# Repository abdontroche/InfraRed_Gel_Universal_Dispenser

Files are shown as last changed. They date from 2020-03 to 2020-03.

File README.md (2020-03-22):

=================================
This project pretends to be a open source device that could help people fighting against the COVID-19.
# Who are we?
*Estimados Miembros: Este grupo está conformado por alumnos, profesores y egresados de la FP-UNA y tiene por objetivo pensar, formular y realizar acciones concretas ante esta situación adversa que vivimos en el país con respecto al coronavirus COVID-19. Iniciamos con gente del área de electrónica e informática pero no estamos cerrados de ninguna manera. El trabajo es voluntario y sin fines de lucro. A hombros de gigantes enfrentaremos mejor las adversidades.*

Dear Members: This group is made up of students, professors and graduates of the FP-UNA and its objective is to think, formulate and carry out concrete actions in the face of this adverse situation that we are experiencing in the country with respect to the COVID-19 coronavirus. We started with people from the electronics and computing area but we are not closed in any way. The work is voluntary and non-profit. On the shoulders of giants we will better face adversities.

Team FP-UNA/COVID

# What we want to achieve?
The board is based on the website called [www.electroschematics.com](www.electroschematics.com) and the project is called [Automatic soap dispenser IR proximity sensor](https://www.electroschematics.com/automatic-soap-dispenser-ir-proximity-sensor/).

We want to use this board and use to dispense gel alcohol adapting it on differents bottles. 

# What we will find inside this repository?

Fist to all we will find the board.

The Board was designed using the software [KiCad 5.1.2](https://www.kicad-pcb.org)

The components are chosen by the existence on the Paraguay electronics componentes market.

## The schmematic

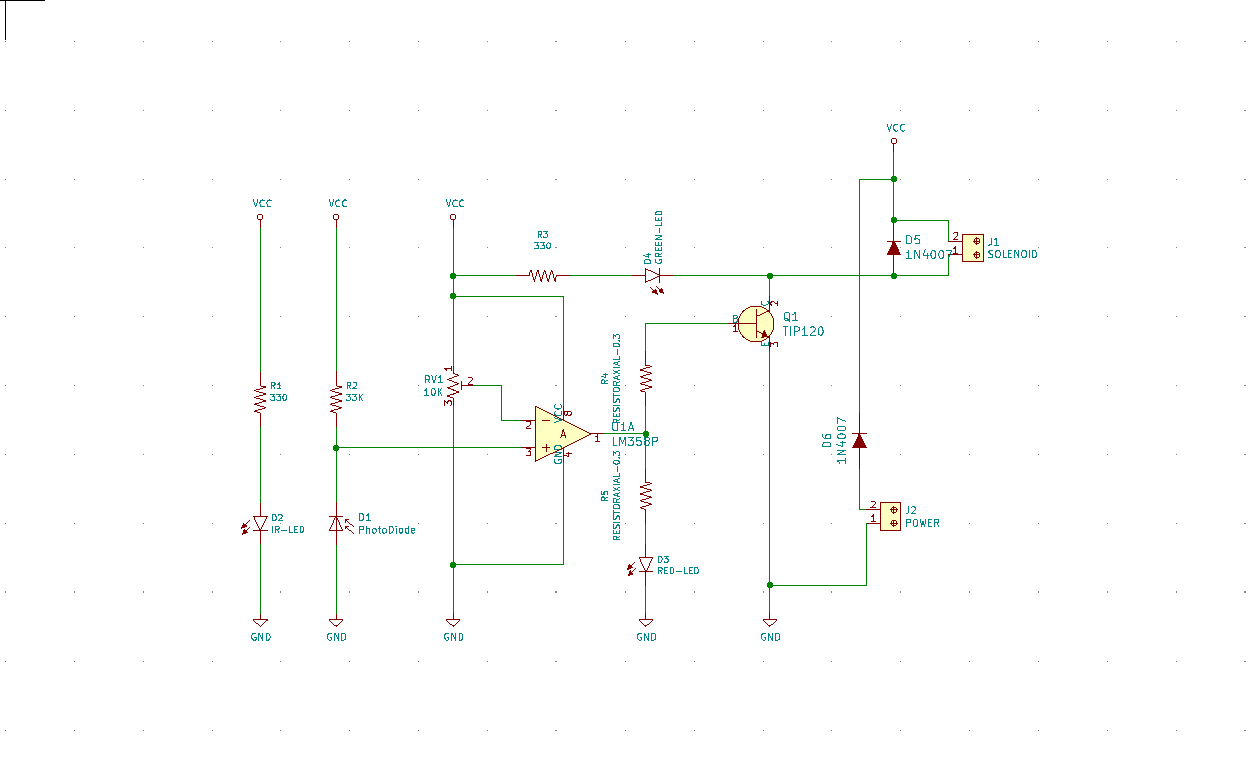
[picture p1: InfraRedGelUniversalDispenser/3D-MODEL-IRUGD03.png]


## The board

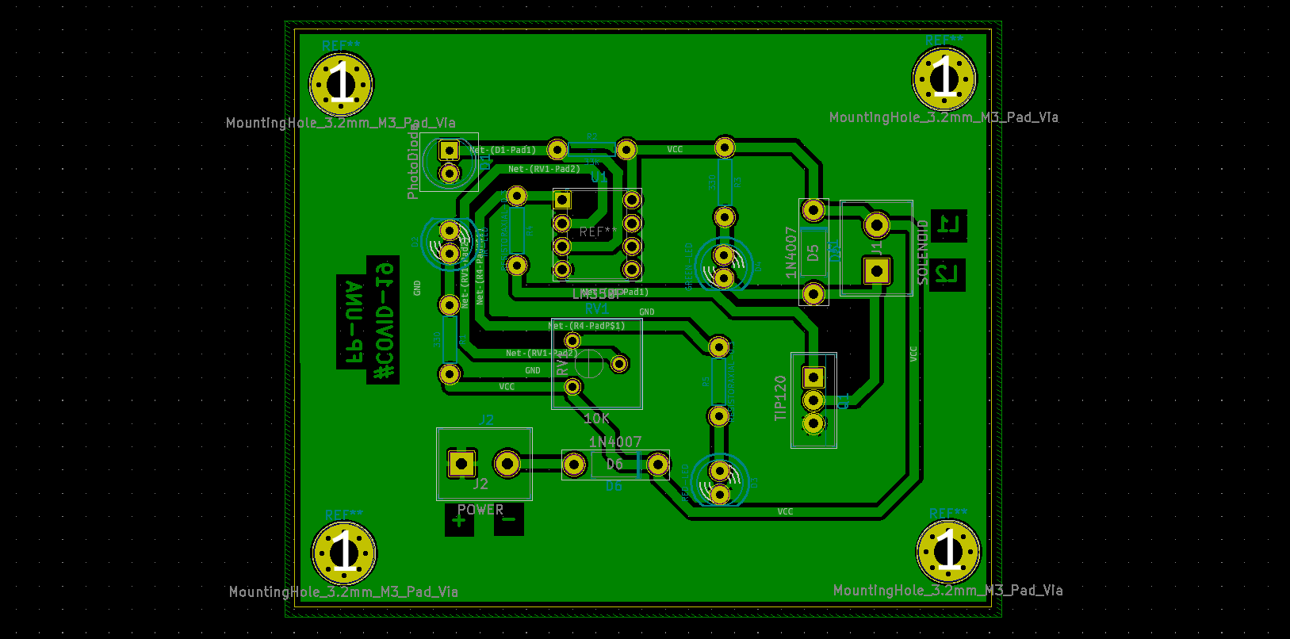
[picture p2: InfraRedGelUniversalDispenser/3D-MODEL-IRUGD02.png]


## Bill Of Materials
This is the file of the [BOM](InfraRedGelUniversalDispenser/bom/ibom.html)
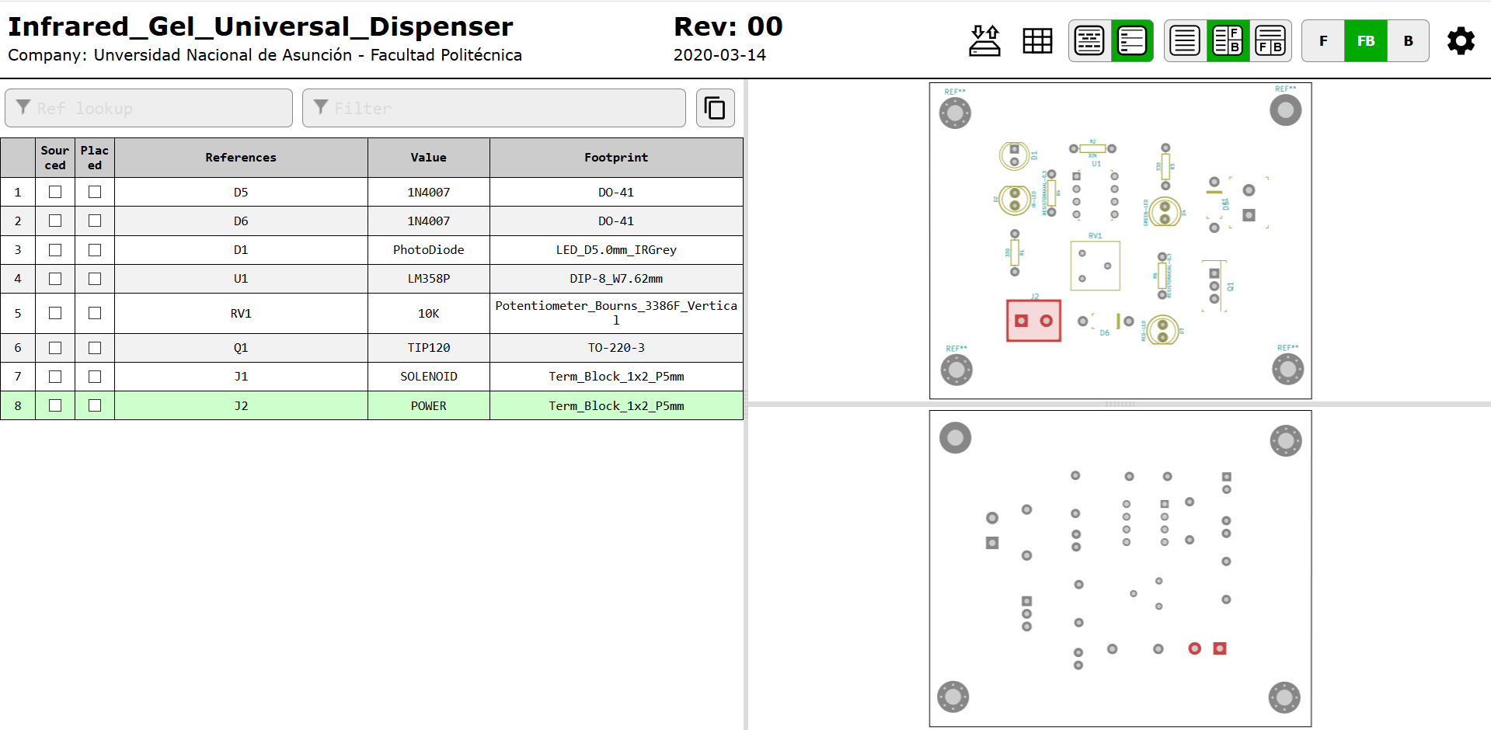
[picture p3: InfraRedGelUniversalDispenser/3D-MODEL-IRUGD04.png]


## The 3D models

You will find the board 3D model in the STP format in order you can choose the software you want to develope the mechanism with.

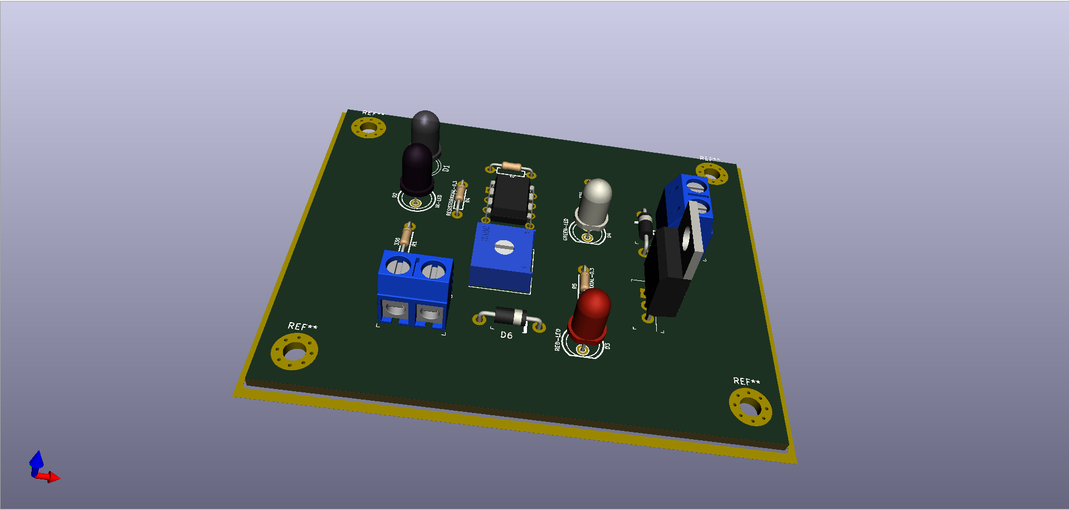
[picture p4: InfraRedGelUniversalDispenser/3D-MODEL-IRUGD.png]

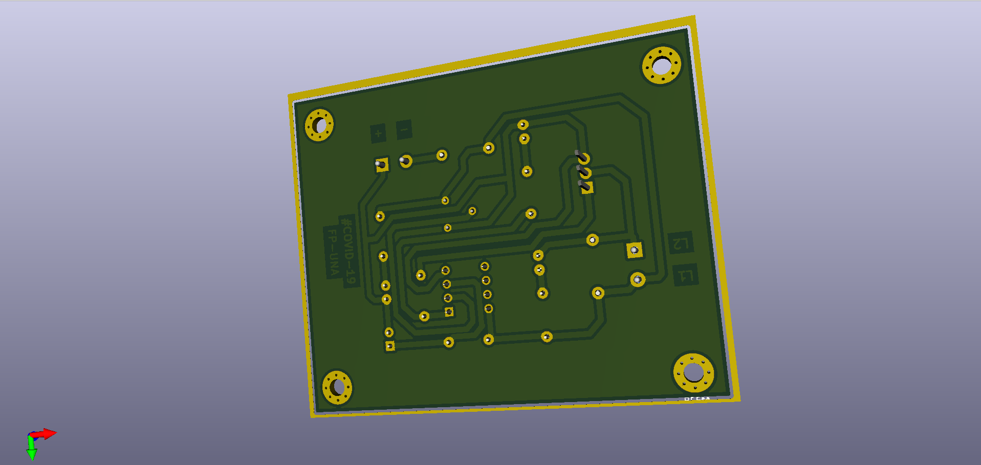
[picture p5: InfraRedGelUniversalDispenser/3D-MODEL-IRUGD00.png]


### Desing the mechanism using [Fusion 360](https://www.autodesk.com/products/fusion-360/students-teachers-educators)

#### Electronic board

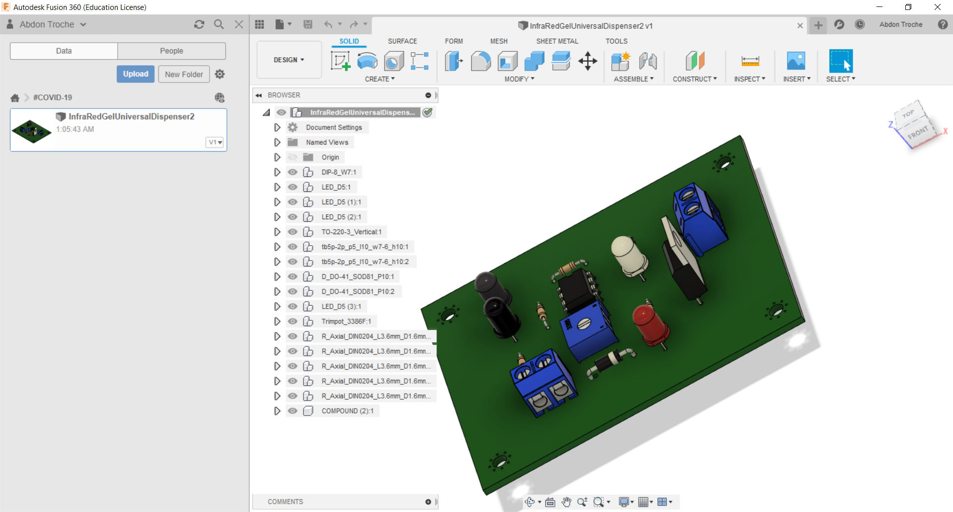
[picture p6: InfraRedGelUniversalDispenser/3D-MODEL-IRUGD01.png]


#### [Dispenser mecanism](InfraRedGelUniversalDispenser/CustomizedSolenoid v5.step)

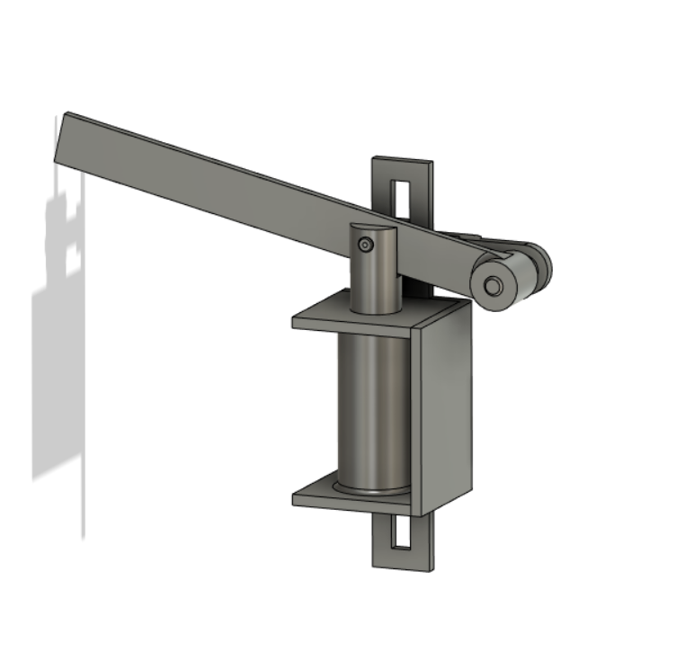
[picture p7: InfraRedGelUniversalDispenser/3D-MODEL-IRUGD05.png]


#### [Gel alcohol bottle or soap bottle dispenser](https://grabcad.com/library/soap-dispenser-5)

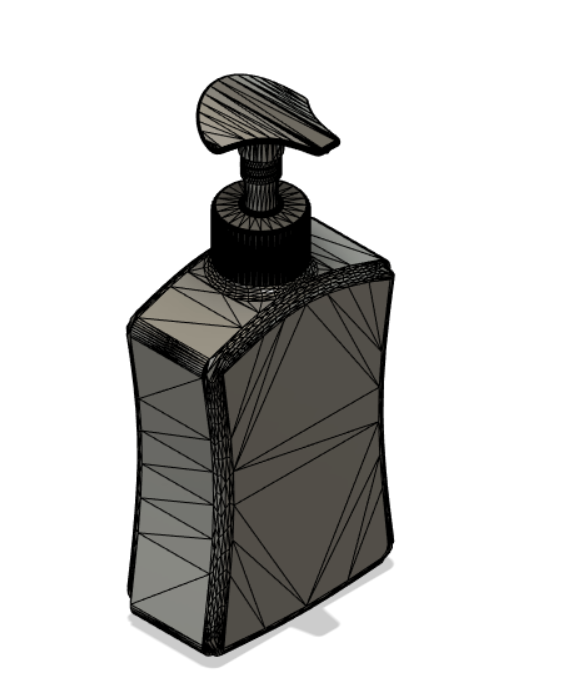
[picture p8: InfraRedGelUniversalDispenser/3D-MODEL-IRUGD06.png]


#### Fisrt assembly

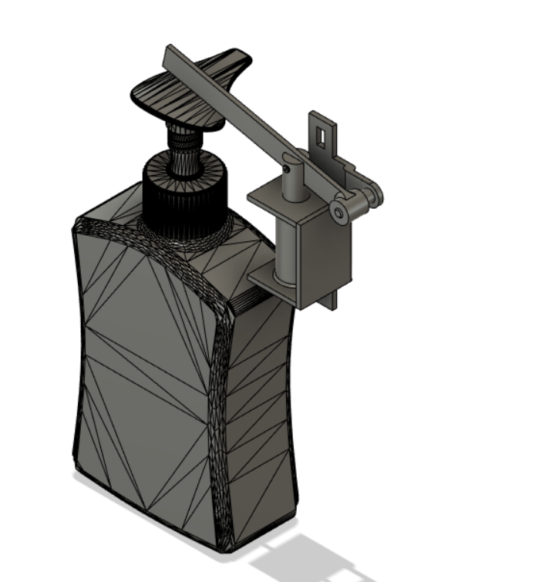
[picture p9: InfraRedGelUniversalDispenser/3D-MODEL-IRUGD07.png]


#### Second assembly

File of the prototipe "InfraRedGelUniversalDispenserDevice v17.step"

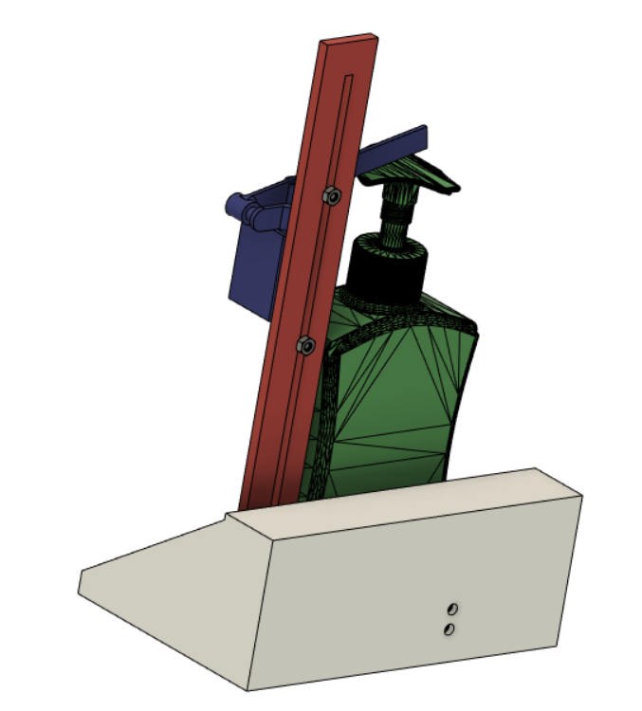
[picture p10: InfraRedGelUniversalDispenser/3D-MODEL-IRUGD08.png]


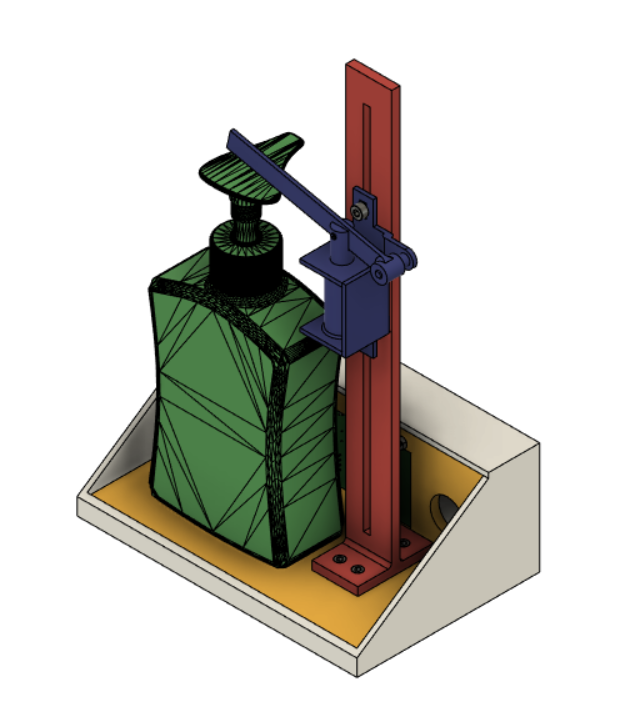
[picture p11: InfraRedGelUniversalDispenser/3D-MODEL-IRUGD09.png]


# This is another version of the board
## The schmematic

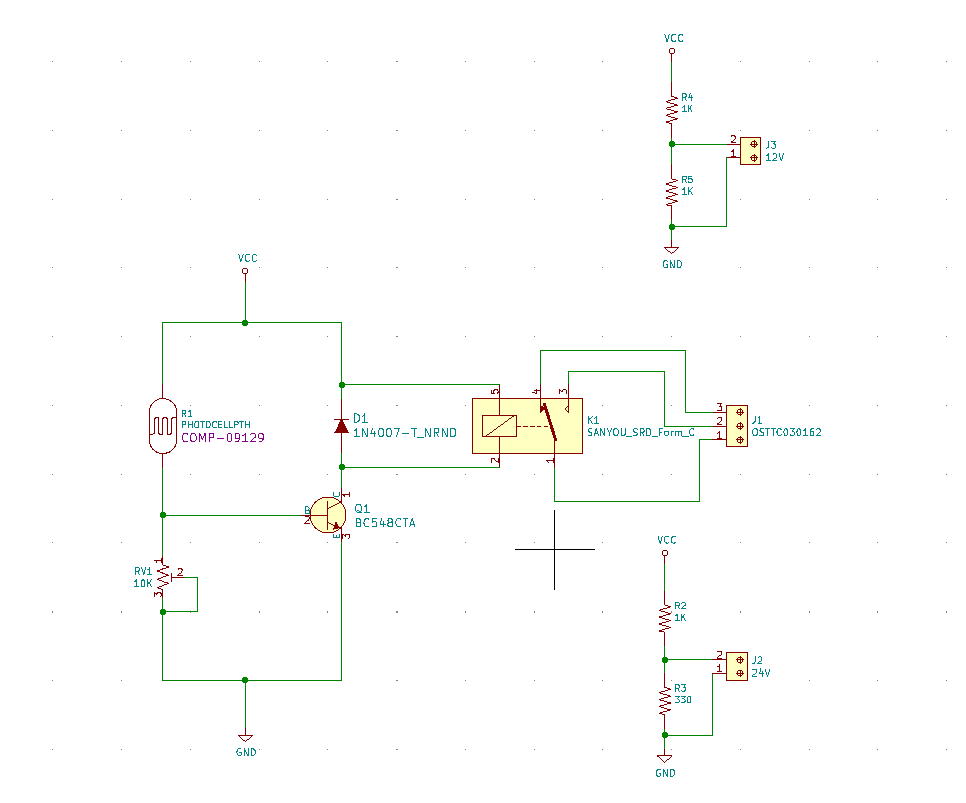
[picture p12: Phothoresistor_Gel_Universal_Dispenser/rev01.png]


## The board

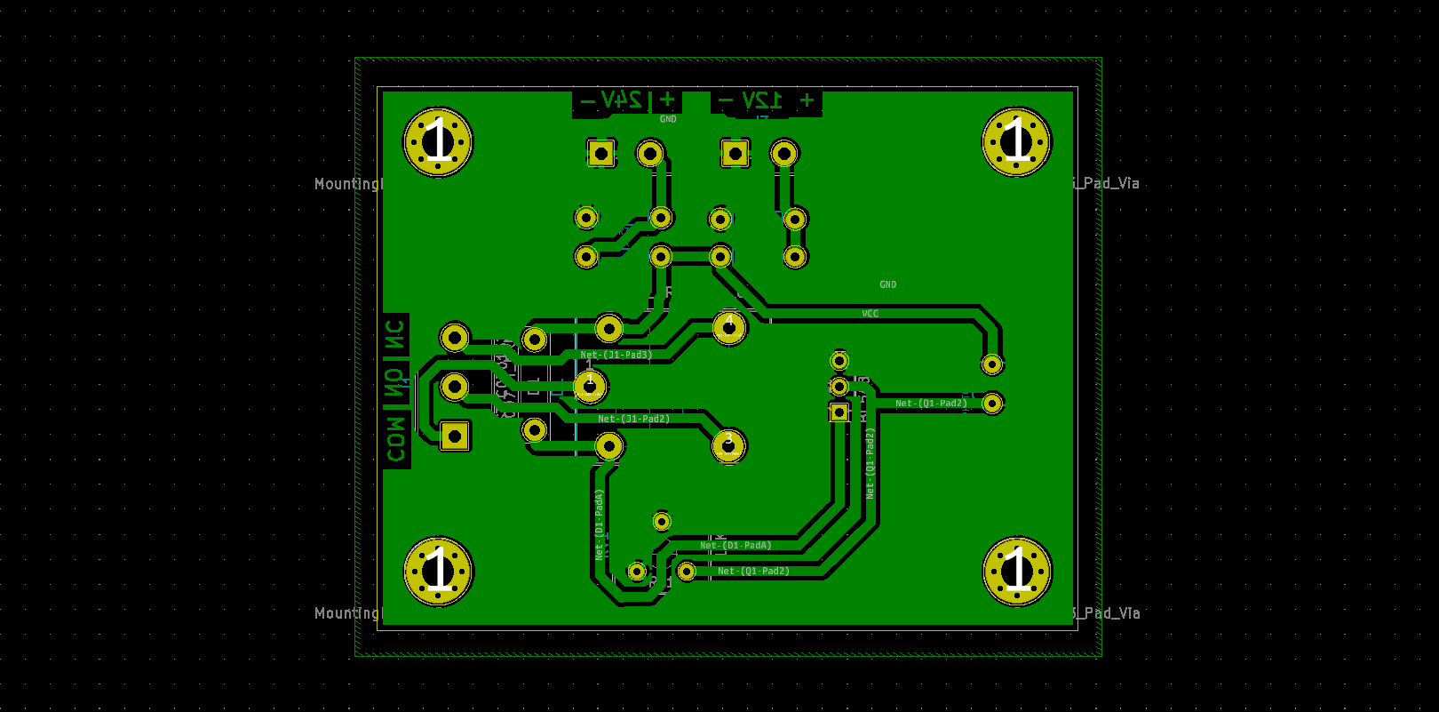
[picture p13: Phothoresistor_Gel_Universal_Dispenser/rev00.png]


## Bill Of Materials

## The 3D models

You will find the board 3D model in the STP format in order you can choose the software you want to develope the mechanism with.

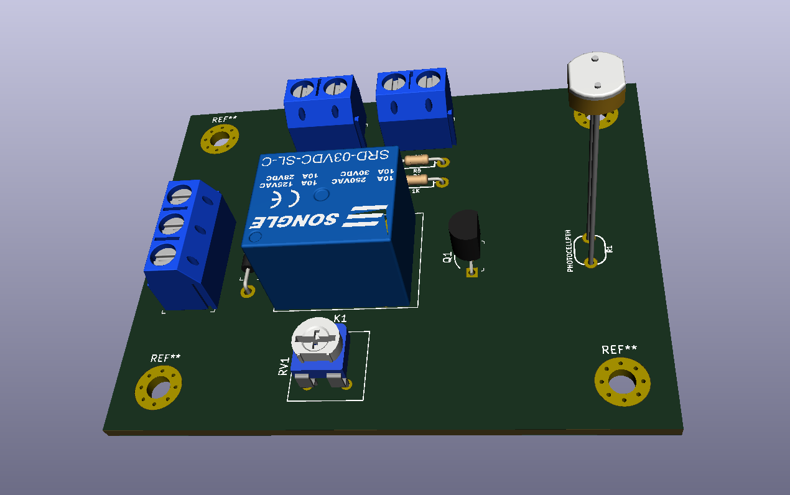
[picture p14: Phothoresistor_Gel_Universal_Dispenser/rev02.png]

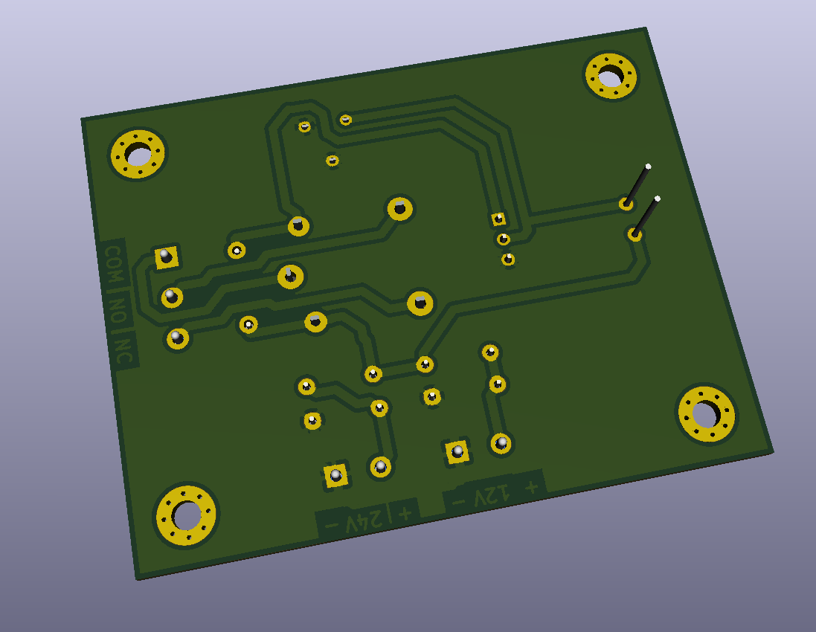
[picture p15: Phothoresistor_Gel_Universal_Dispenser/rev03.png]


### Desing the mechanism using [Fusion 360](https://www.autodesk.com/products/fusion-360/students-teachers-educators)

#### Electronic board

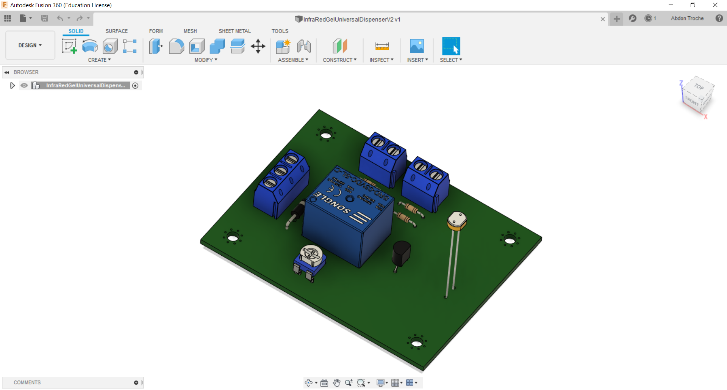
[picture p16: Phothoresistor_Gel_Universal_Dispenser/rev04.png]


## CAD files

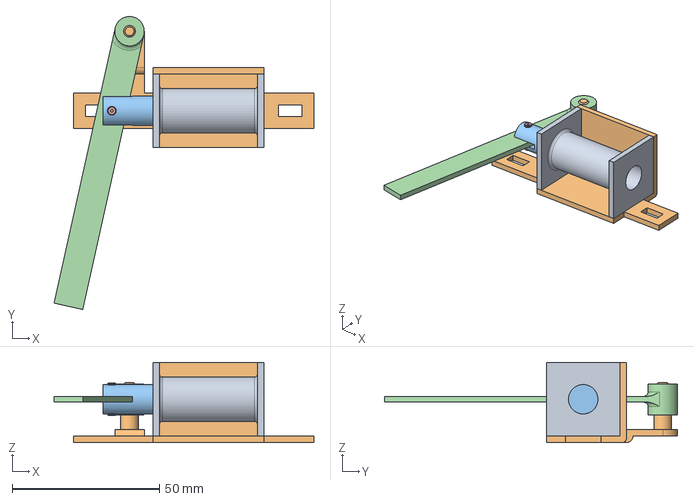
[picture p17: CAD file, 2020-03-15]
InfraRedGelUniversalDispenser/CustomizedSolenoid v5.step
88.2 x 99.4 x 27.2 mm

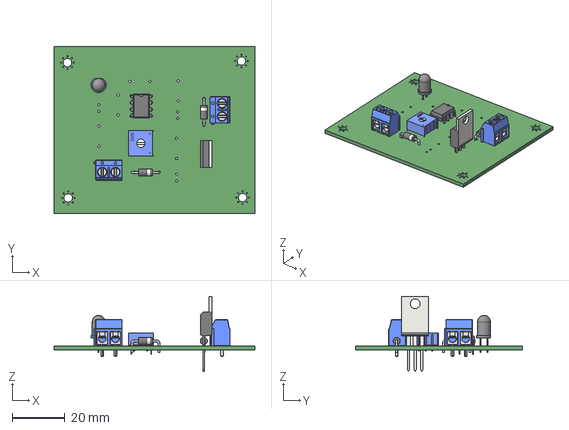
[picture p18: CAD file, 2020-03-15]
InfraRedGelUniversalDispenser/InfraRedGelUniversalDispenser.step
76.4 x 63.3 x 28.5 mm

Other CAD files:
InfraRedGelUniversalDispenser/InfraRedGelUniversalDispenser2 v1.f3d
Phothoresistor_Gel_Universal_Dispenser/Phothoresistor_Gel_Universal_Dispenser.f3d

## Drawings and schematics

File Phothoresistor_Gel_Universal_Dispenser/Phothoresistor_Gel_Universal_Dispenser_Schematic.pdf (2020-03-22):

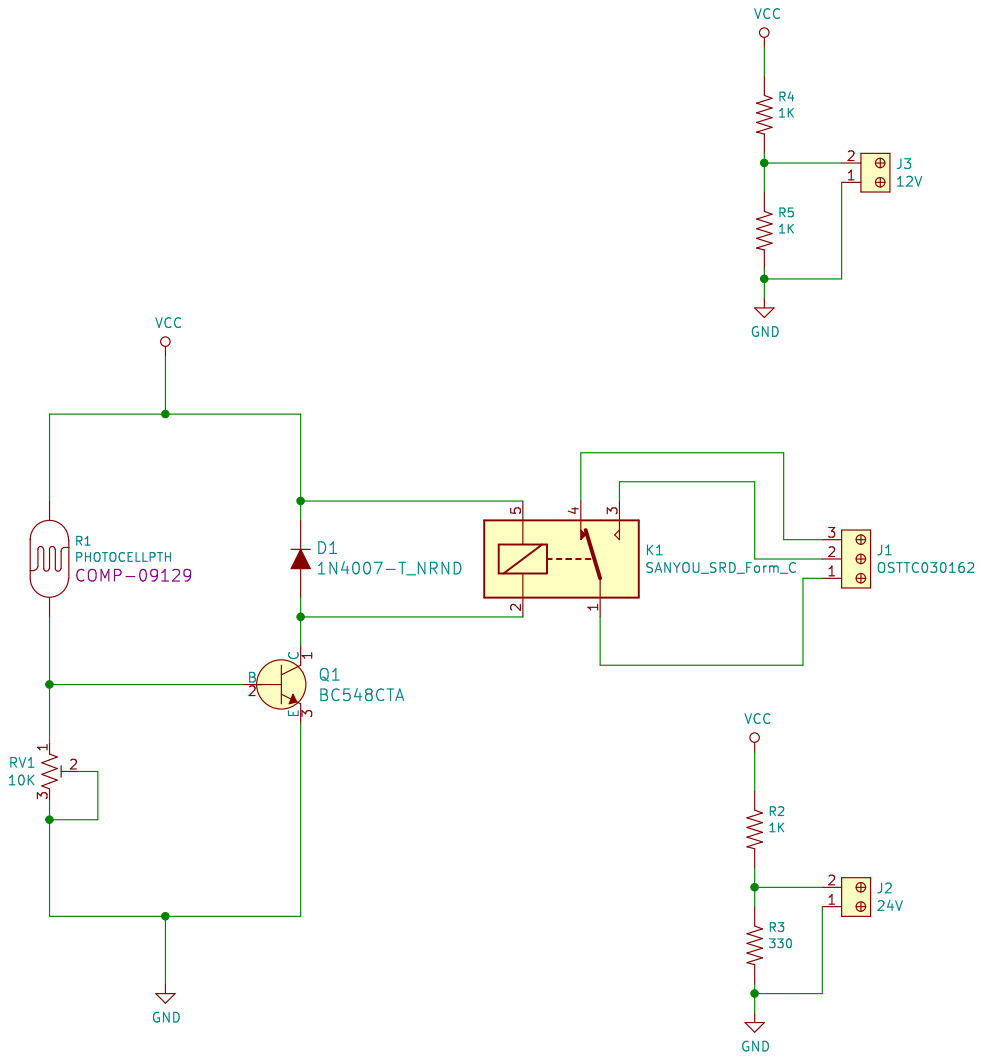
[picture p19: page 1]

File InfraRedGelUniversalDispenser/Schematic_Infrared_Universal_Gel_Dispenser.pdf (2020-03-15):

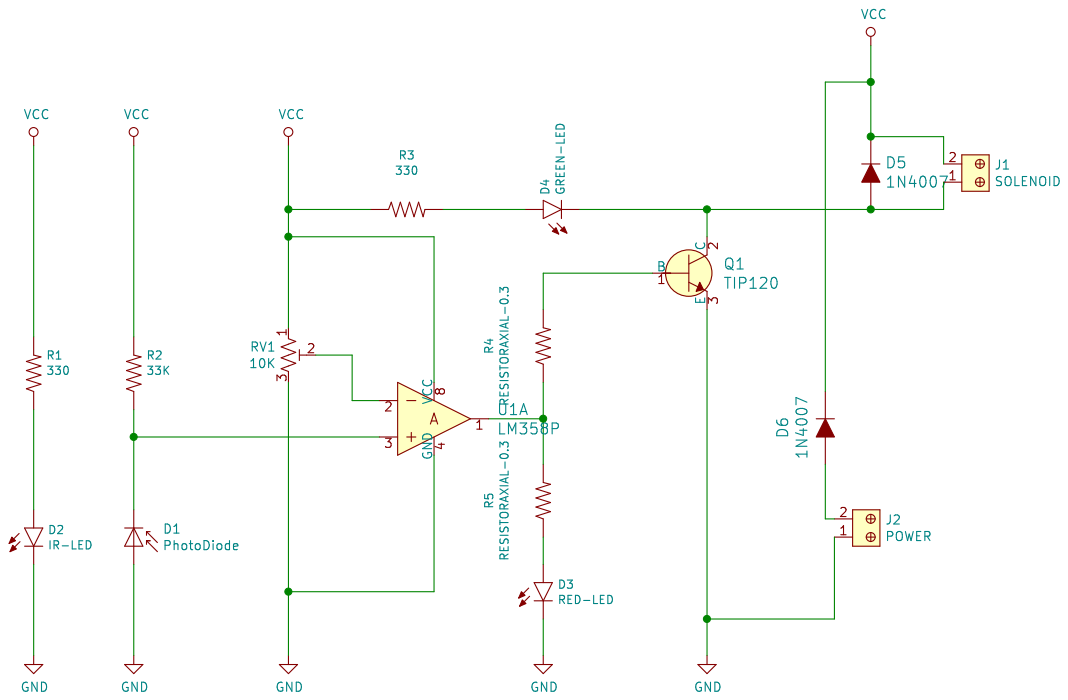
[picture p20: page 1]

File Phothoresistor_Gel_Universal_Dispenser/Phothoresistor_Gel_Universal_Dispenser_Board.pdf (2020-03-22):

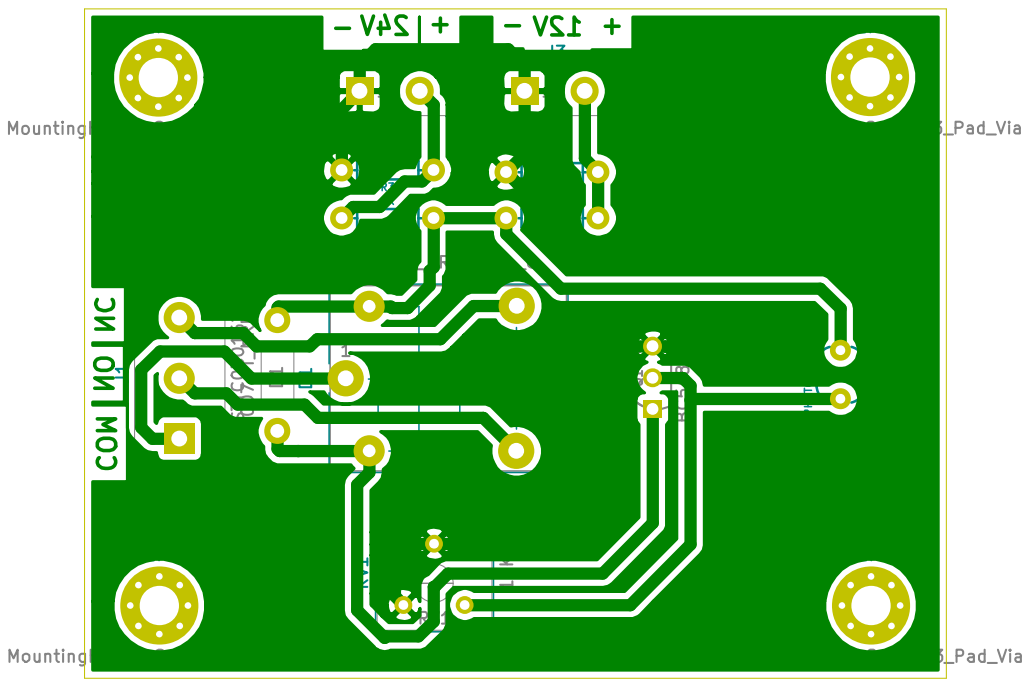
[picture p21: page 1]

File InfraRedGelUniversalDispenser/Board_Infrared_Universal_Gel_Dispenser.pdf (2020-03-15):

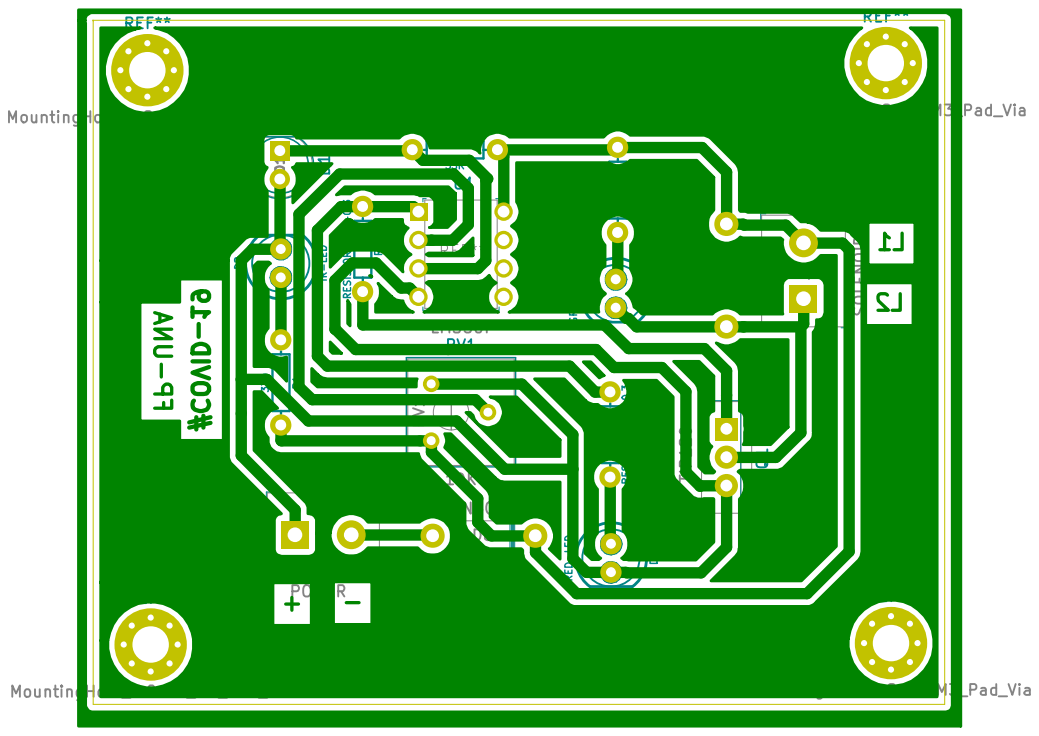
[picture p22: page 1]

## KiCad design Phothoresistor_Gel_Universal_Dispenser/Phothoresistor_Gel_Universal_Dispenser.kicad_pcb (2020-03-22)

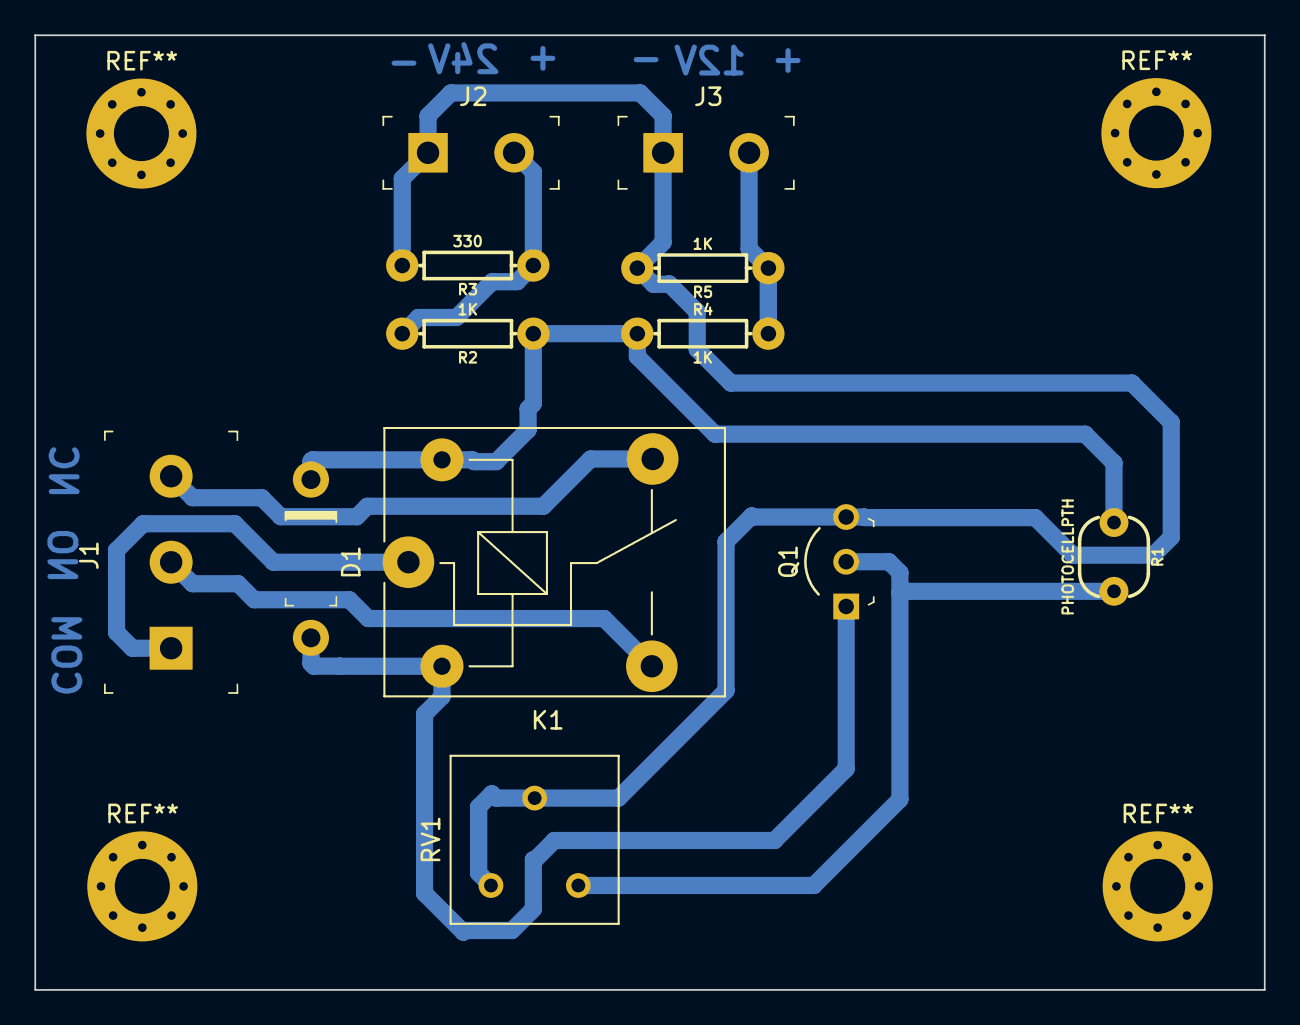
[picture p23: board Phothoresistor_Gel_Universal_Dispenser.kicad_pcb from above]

Board: 2 copper layers, 71.5 x 55.5 mm, 12 parts (0 on the bottom side), 9 nets.

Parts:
D1: 1N4007-T_NRND; DO-41
J1: OSTTC030162; Term_Block_1x3_P5mm
J2: 24V; Terminal_Block_D1.3mm_P5mm
J3: 12V; Terminal_Block_D1.3mm_P5mm
K1: SANYOU_SRD_Form_C; Relay_SPDT_SANYOU_SRD_Series_Form_C
Q1: BC548CTA; TO-92-3_Formed_Leads
R1: PHOTOCELLPTH; PHOTOCELL
R2, R4, R5: 1K; AXIAL-0.3
R3: 330; AXIAL-0.3
RV1: 10K; Potentiometer_Bourns_3386F_Vertical

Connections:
GND: J2.1, J3.1, Q1.3, R3.P$2, R5.P$2, RV1.2, RV1.3
unnamed: D1.A, K1.2, Q1.1
unnamed: J1.1, K1.1
unnamed: J1.2, K1.3
unnamed: J1.3, K1.4
unnamed: J2.2, R2.P$2, R3.P$1
unnamed: J3.2, R4.P$2, R5.P$1
unnamed: Q1.2, R1.2, RV1.1
VCC: D1.K, K1.5, R1.1, R2.P$1, R4.P$1

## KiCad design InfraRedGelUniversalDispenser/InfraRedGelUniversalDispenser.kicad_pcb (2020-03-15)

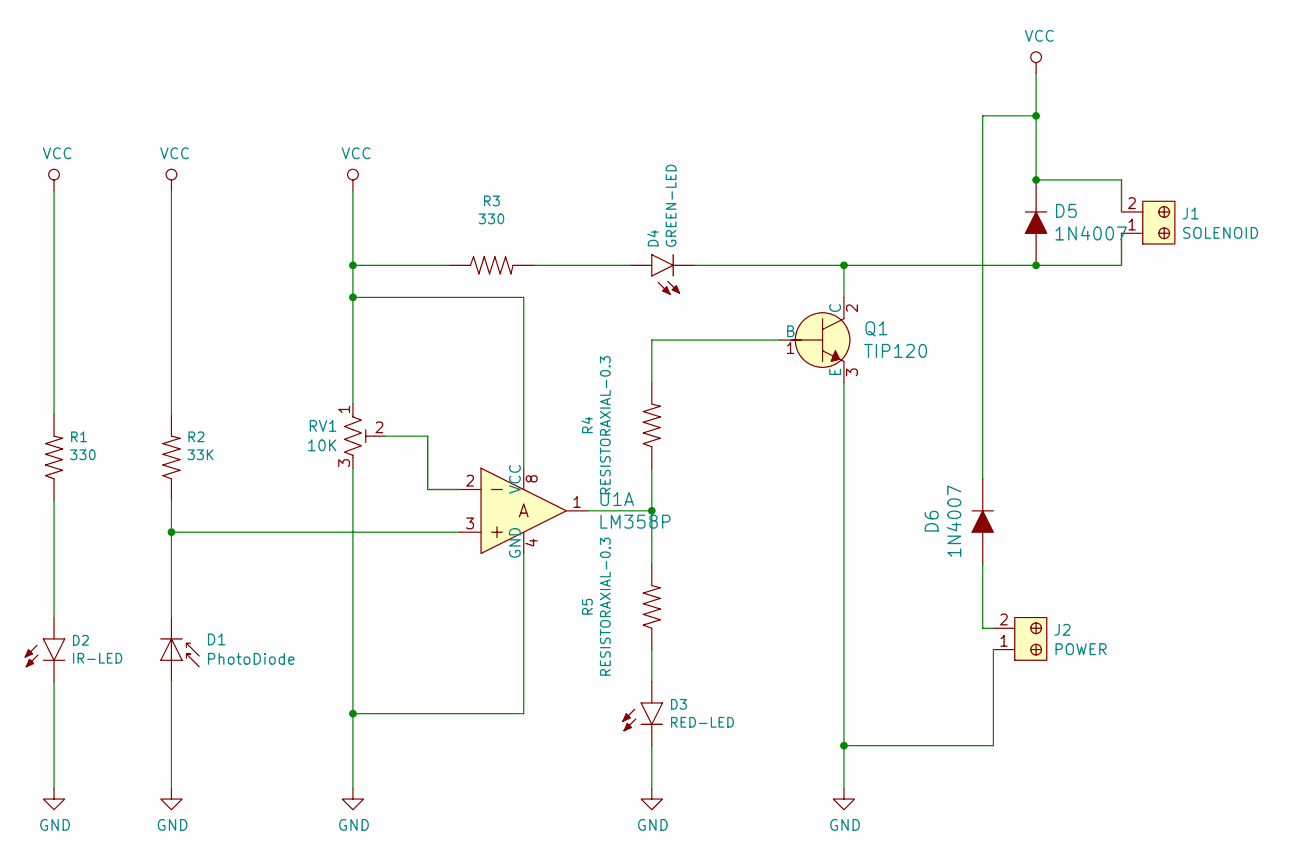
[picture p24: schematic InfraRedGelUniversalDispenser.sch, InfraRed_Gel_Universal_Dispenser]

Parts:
D1: PhotoDiode; LED_D5.0mm_IRGrey
D2: IR-LED; LED_5MM-KIT
D3: RED-LED; LED_5MM-KIT
D4: GREEN-LED; LED_5MM-KIT
D5, D6: 1N4007; DO-41; MPN 1N4007-T; Digi-Key_PN 1N4007DICT-ND
J1: SOLENOID; Term_Block_1x2_P5mm; MPN OSTTC020162; Digi-Key_PN ED2600-ND
J2: POWER; Term_Block_1x2_P5mm; MPN OSTTC020162; Digi-Key_PN ED2600-ND
Q1: TIP120; TO-220-3; MPN TIP120; Digi-Key_PN 497-2539-5-ND
R1, R3: 330; AXIAL-0.3
R2: 33K; AXIAL-0.3
R4, R5: RESISTORAXIAL-0.3; AXIAL-0.3
RV1: 10K; Potentiometer_Bourns_3386F_Vertical
U1: LM358P; DIP-8_W7.62mm; MPN LM358P; Digi-Key_PN 296-1395-5-ND

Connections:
GND: D1.2 (A), D2.K (C), D3.K (C), J2.1, Q1.3 (E), RV1.3, U1.4 (GND)
unnamed: D1.1 (K), R2.P$1 (1), U1.3
unnamed: D2.A, R1.P$1 (1)
unnamed: D3.A, R5.P$1 (1)
unnamed: D4.A, R3.P$2 (2)
unnamed: D4.K (C), D5.A, J1.1, Q1.2 (C)
unnamed: D6.A, J2.2
unnamed: Q1.1 (B), R4.P$2 (2)
unnamed: R4.P$1 (1), R5.P$2 (2), U1.1
unnamed: RV1.2, U1.2
VCC: D5.K, D6.K, J1.2, R1.P$2 (2), R2.P$2 (2), R3.P$1 (1), RV1.1, U1.8 (VCC)

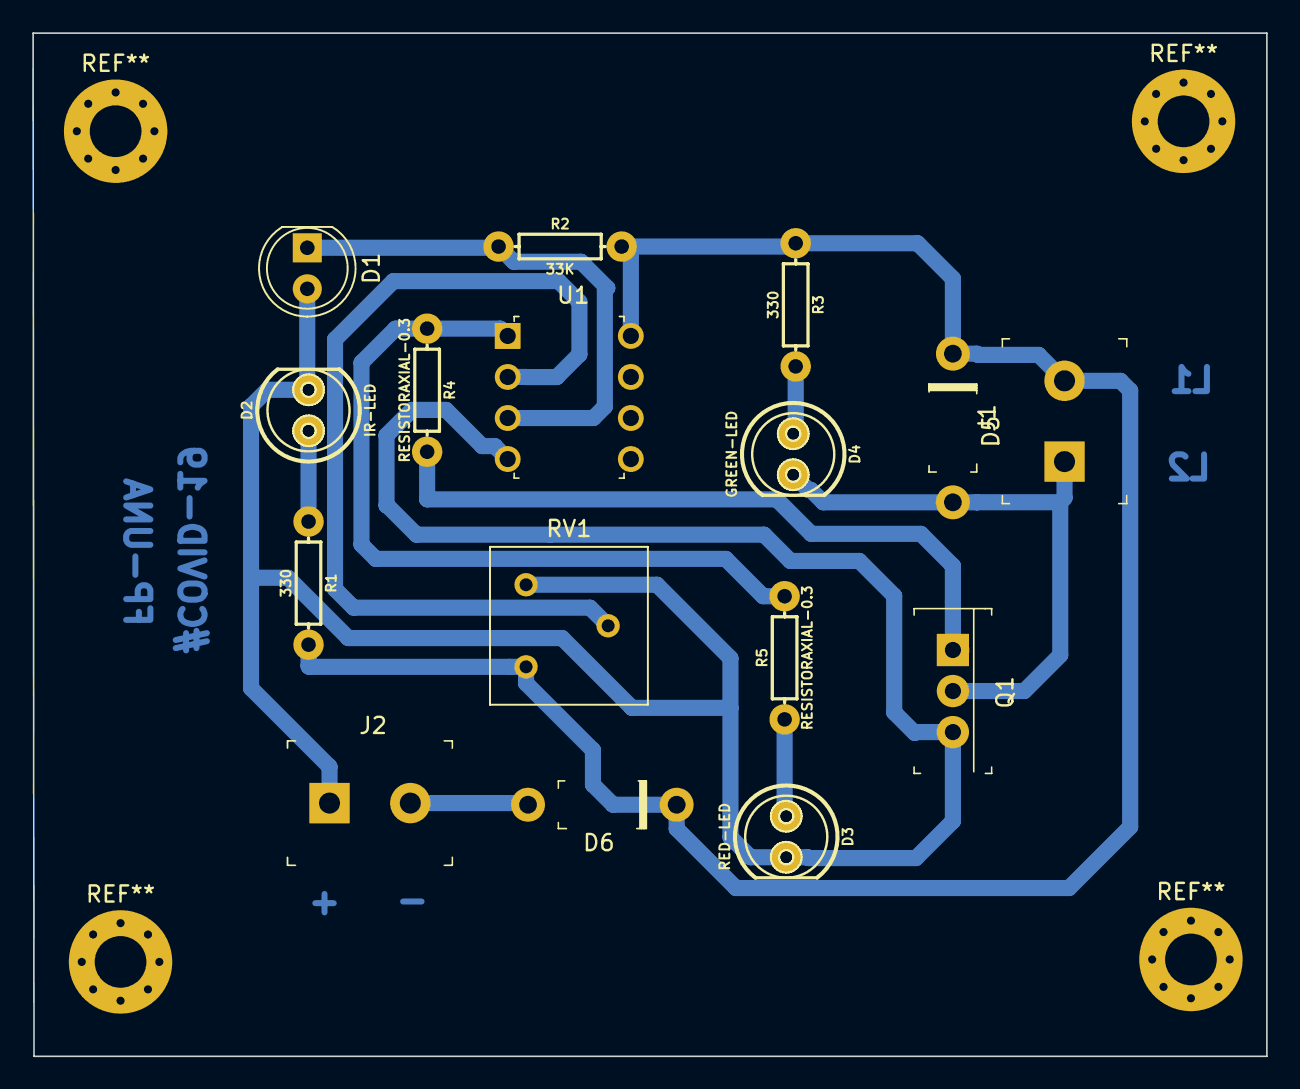
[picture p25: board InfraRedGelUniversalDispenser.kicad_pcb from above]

Board: 2 copper layers, 76.4 x 63.3 mm, 16 parts (0 on the bottom side), 11 nets.

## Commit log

2020-03-15 I added all the files related to the opensource project called InfraredUniversalGelDispenserDevice
    [InfraRedGelUniversalDispenser.kicad_pcb, InfraRedGelUniversalDispenser.sch, InfraRedGelUniversalDispenser.step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]
2020-03-15 I added description to the readme in orther to make easy the reading to any who wants to work in the project
    [InfraRedGelUniversalDispenser-B_Cu.gbr, InfraRedGelUniversalDispenser-B_Mask.gbr, InfraRedGelUniversalDispenser-B_Paste.gbr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]
2020-03-15 I created the mechanism for the dispenser and also generated the bill of materials for make the budget
    [CustomizedSolenoid v5.step]
2020-03-16 I finished the prototipe of the device and it is ready for fabrication
2020-03-22 I designed a new version of the sensor with LDR simpler than the last one
    [InfraRedGelUniversalDispenserV2-B_Cu.gbr, InfraRedGelUniversalDispenserV2-B_Mask.gbr, InfraRedGelUniversalDispenserV2-B_Paste.gbr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]
2020-03-22 I added readme information about the new version of the board

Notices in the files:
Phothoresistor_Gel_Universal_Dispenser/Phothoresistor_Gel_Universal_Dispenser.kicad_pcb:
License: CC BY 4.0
